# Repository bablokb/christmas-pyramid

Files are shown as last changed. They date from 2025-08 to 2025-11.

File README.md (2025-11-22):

A 3D-printed, Motor-driven Christmas Pyramid
============================================

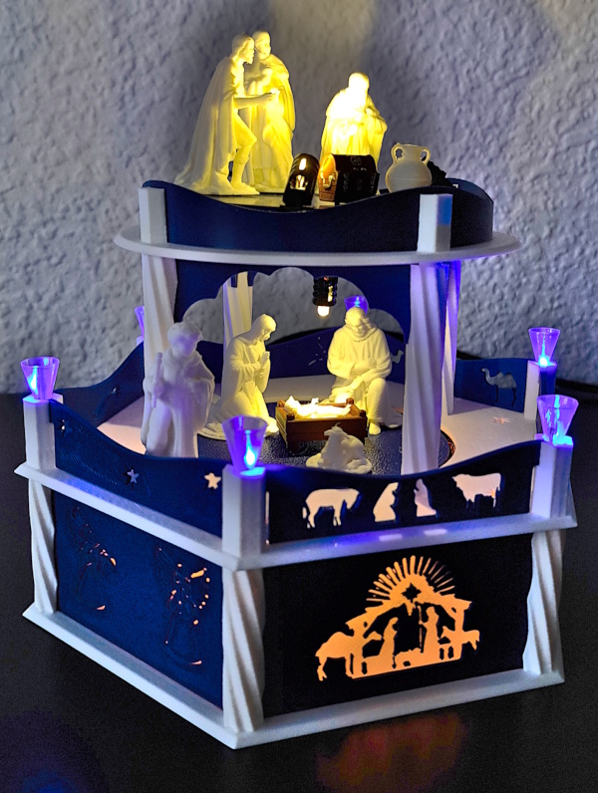
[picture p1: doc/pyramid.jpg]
pyramid.mp4


Introduction
------------

This project is about building a christmas pyramid with a motor driven
turntable, lightning and music (click on the image above to see it in
action). There are three distinct parts: the electronics, the software
and the 3D-design. A fourth part, a selfmade pcb is also available,
but not necessary. I only use it because it minimizes cables.

The electronics uses cheap parts that are widely available. The software is
implemented in CircuitPython and mostly portable. The 3D build uses
easy to print parts that can be assembled without glue.

Besides the "big" version with multiple levels, a simplified version is
also available:

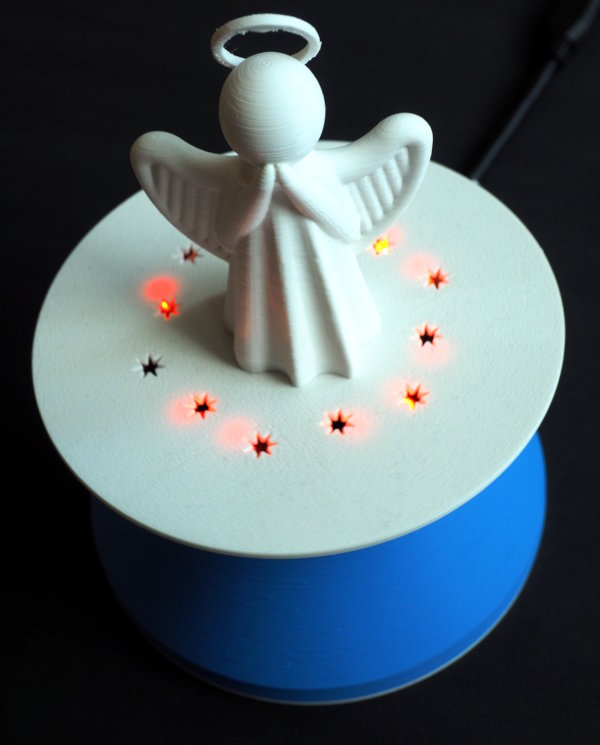
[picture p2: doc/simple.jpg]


This version only has three printed parts: the base, the wall and the
plate. It uses a neopixel-ring instead of LEDs, otherwise
it uses the same electronics as the normal version of the pyramid.

Details
-------

Read about

  - [Electronics](./doc/electronics.md)
  - [Software](./doc/software.md)
  - [3D-Printing](./doc/printing.md)
  - [Support-PCB](./doc/pcb.md)

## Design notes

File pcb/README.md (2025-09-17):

KiCAD Source Files for the Support PCB
======================================

For details, read [pcb.md](../doc/pcb.md).

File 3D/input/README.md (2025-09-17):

This file contains a number of remixes of existing models (see
[printing](../doc/printing.md)).

All models were flattened, centered and scaled for use as silhouttes
and cutouts for walls and fences.

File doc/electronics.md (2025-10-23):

Electronics
===========

The Motor
---------

The turntable is driven by a small 28BYJ-48 stepper motor (5V
version). Stepper motors are actually not the first choice for
continuous rotation, but since we need very low rpm values, this
option simplfies things. Another advantage is the fact that we can
drive this motor with 5V, so we only need a single power supply for
the motor and the microcontroller board.

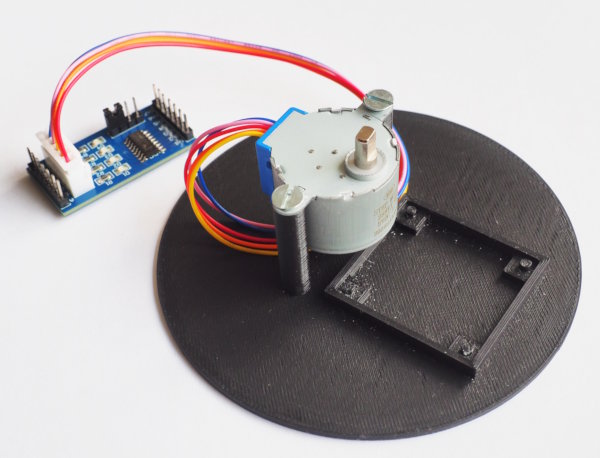
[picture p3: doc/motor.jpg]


The motor needs a driver board. It is usually sold together with an
uln2003a board. Make sure to buy the "blue" version with all seven
pins broken out. The board has seven channels, four of them are
necessary for the motor. The remaining three channels can be used to
drive LEDs.

Both the "blue" as the "green" driver boards have four useless LEDs
that blink when the mcu sends data. If necessary, just remove the LEDs
e.g. with pliers.

If you want to turn more than one level, you probably need a stronger
motor, e.g. a NEMA-17. Those motors also need a different voltage and
a different driver board. In this case it is better to supply the 5V
for the microcontroller from a step-down board.

The motor does not have to be in the center of the turntable but you
will need gears if not. OpenSCAD has a gears library that might be
useful in this case.

Lighting
--------

There are many options available to add some lighting. This implementation
uses three channels of the uln200a to drive 5V LEDs. Basic illumination
for the silhouettes uses standard 3mm LED-strips cut to the right length
(they can be cut and soldered every 25mm).

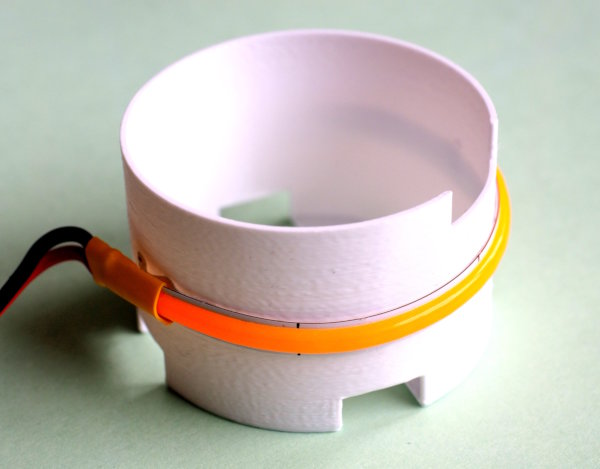
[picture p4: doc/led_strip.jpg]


For the remaining lights, normal flicker-LEDs are a good choice. They are
available pre-assembled with resistor and cables. Another option are
components from a Lego lighting kit. The LEDs use very thin wires which
makes assembly easy. The drawback are the connectors they use. It
is not trivial to attach them to a normal devboard, and even
attaching them to standard (lego-lighting) components is fiddly.

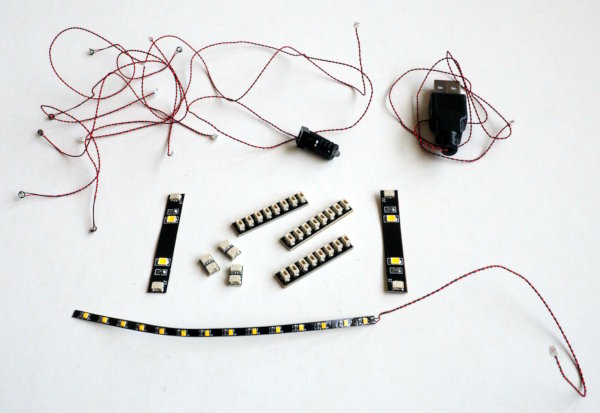
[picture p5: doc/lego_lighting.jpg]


The pyramid in this project makes heavy use of them to distribute
power to the upper levels through hallow posts.

Music
-----

The recommandation for music is to use a [DFPlayer
Mini](https://wiki.dfrobot.com/DFPlayer_Mini_SKU_DFR0299). This
breakout is not much larger than a SD-reader. It has a MP3-decoder and
an amplifier on board. The autonomous player takes load off the
microcontroller.  Two IOs enable basic operation (next/previous song
and volume up/down). All functions can be controlled using
UART-commands. Libraries for the DFPlayer are available for every
relevant language.

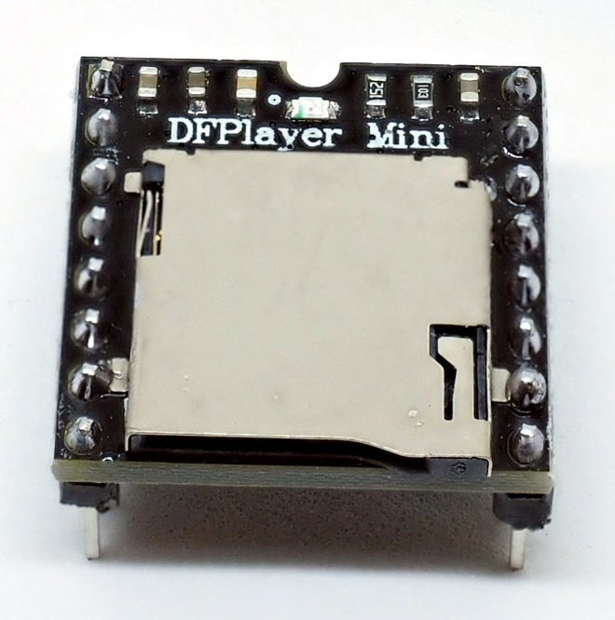
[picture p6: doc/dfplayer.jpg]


It seems that there are different version of the DFPlayer Mini around,
some are counterfeits. Problems with initialization have been
reported. On some (old?!) versions random playback does not seem to
work.

The alternative is to decode the MP3 in the microcontroller and output
I2S to a small I2S-DAC (e.g. the MAX98357A). While this does works it
has a number of drawbacks. At least with the ESP32-S2 which I use the
motor tends to stutter. A faster processor might not have this
problem. The second drawback is the larger number of pins needed (four
for the SD-card, four for the I2S-DAC and some more for buttons if you
want to control the playback). And finally a SD-breakout plus
amplifier is more expensive than the DFPlayer and both together need
two times the physical space.

The Microcontroller
-------------------

The mcu must provide enough digital IO pins and must be fast
enough. Something like the Pico should be fine. Depending on your
setup, you need

  - motor: 4 IO-pins
  - LEDs: 0-3 IO-pins
  - DFPlayer: 2 UART pins
  - Buttons: 3 IO pins

Since the DFPlayer provides two IOs, the IOs for the three buttons will
control the turntable speed (slower/faster) and pause the audio.
If you want to control more functions, you need more.

This project uses the Lolin-S2 Mini. It provides many pins on a small
footprint. As an added bonus, it could act as a webserver to enable
remote control via an app. This is an option that is not implemented.

Further Reading
---------------

Head on to [Software](./software.md) to read about the how to
drive the hardware.

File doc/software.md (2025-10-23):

The Software
============

The software is implemented in CircuitPython, but porting it to other
languages (especially MicroPython) should be straight forward.

The provided source-code is agnostic about the microprocessor that is
used. Since CircuitPython supports many different processors, you are
free to pick what you want (as long as you have enough IO-pins).

Read the section about configuration below to adapt the software to your
specific setup.

Installation
------------

Just copy everything below `src/` to your device. Note that `src/lib`
contains a number of precompiled libraries:

  - adafruit_pixelbuf
  - adafruit_ticks
  - asyncio
  - neopixel

These are CircuitPython version 9 libraries (also compatible
with version 10). You might want to update these libraries if you have
problems (the recommended way is to use circup).

Configuration
-------------

Use `src/config_pcb.py` or `src/config_breadboard.py` as a template
for your own configuration and change the import in `src/main.py`
accordingly.

Implementation Notes
--------------------

The hardware components (Motor, LEDs, music and buttons) are wrapped
by simple classes and controlled by asynchronous tasks. The main
program does not do much more than instantiating a task for every
hardware component and then starting all of them in parallel.

    motor = Motor(config.PINS_MOTOR,
                  config.GEAR_RATIO,
                  config.DIRECTION,
                  config.RPM,
                  config.DEBUG)
    player = Player(config.PINS_UART, config.VOLUME, config.DEBUG)
    buttons = Buttons(config.PINS_BUTTON, config.PINS_CB,
                      motor, player, config.DEBUG)
    leds = Leds(config.PINS_LED, config.DUTY_LED, config.DEBUG)

    stop_event = asyncio.Event()
    atexit.register(at_exit,stop_event,player)

    # start controller tasks and wait for end
    await asyncio.gather(buttons.run(0,stop_event),
                         motor.run(0,stop_event),
                         player.run(0.2,stop_event),
                         leds.run(0.5,stop_event)
                         )

As you can see, there is a stop-event that is triggered during
exit-processing in case of any exception (like a
keyboard-interrupt). This s useful for software development, sind in a
productive environment, stopping is done simply by pulling the power-plug.

The tasks themselves are also simple. The motor task for example just
starts the motor and then waits for the stop-event:

    async def run(self, delay, stop_event):
      """ create motor task """

      await asyncio.sleep(delay)
      self._motor = uln2003a.Uln2003aFullStep(*self._pins,
                                              self._gear_ratio,
                                              debug=self._debug)
      asyncio.create_task(self._motor.rotate(self._direction,self._rpm))
      await stop_event.wait()
      self._motor.stop()
      self._motor.deinit()

The button class uses the `keypad`-module from core CircuitPython
to catch and process any buttons that are pressed. The other wrapper
classes provide callbacks that are directly executed from the button-task.

The lighting uses a slightly modified version of the LED-animation
library from <https://github.com/jandelgado/jled-circuitpython>.

The libraries for the DFPlayer and the motor are from myself, see
<https://github.com/bablokb/circuitpyton-dfplayer> and
<https://github.com/bablokb/circuitpyton-uln2003a>.

Porting
-------

For MicroPython, porting should be simple. The DFPlayer library of
this project is a port of a MicroPython library. For the uln2003a you
will also find existing MicroPython libs, but AFAIK these do not support
async operations. A suitable LED-animation library should also be
available.

For C (Arduino) the situation should be similar. The original source
code of DFRobot for the DFPlayer was written for Arduino (but there
are others as well). The LED-animation library used in this project is
also available in a C version. And support for the uln2003 is also
available.

Further Reading
---------------

Head on to [3D-Printing](./printing.md) to read about the how the
pyramid is printed and assembled.

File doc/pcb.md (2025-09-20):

Support PCB for Electronic Components
=====================================

This PCB allows you to put all components on a small footprint.

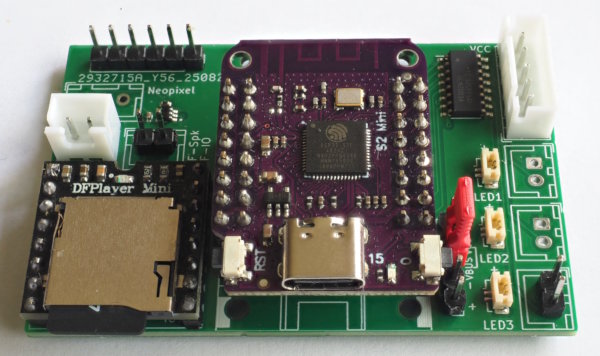
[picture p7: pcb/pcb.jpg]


On board:

  - uln2003a motor driver
  - level-shifter for a strand of neo-pixels
  - 3 SURS connectors for Lego-lighting

Connectors (THT):

  - Motor (JST-XH)
  - 3xLED (JST-XH)
  - Lolin S2-Mini
  - DFPlayer Mini
  - Speaker
  - 2 IOs from DFPlayer
  - 1x6 header with GND + 5 IOs (for external buttons)
  - 2x5 header with 2xGND, 2x3V3 + 6 IOs
  - 1x Grove I2C

This project neither uses the neo-pixel, the I2C-connector or the
optional 2x5 IO-header.

In the directory `production_files` you have ready to deploy files
for JLCPCB.

Schematic
---------

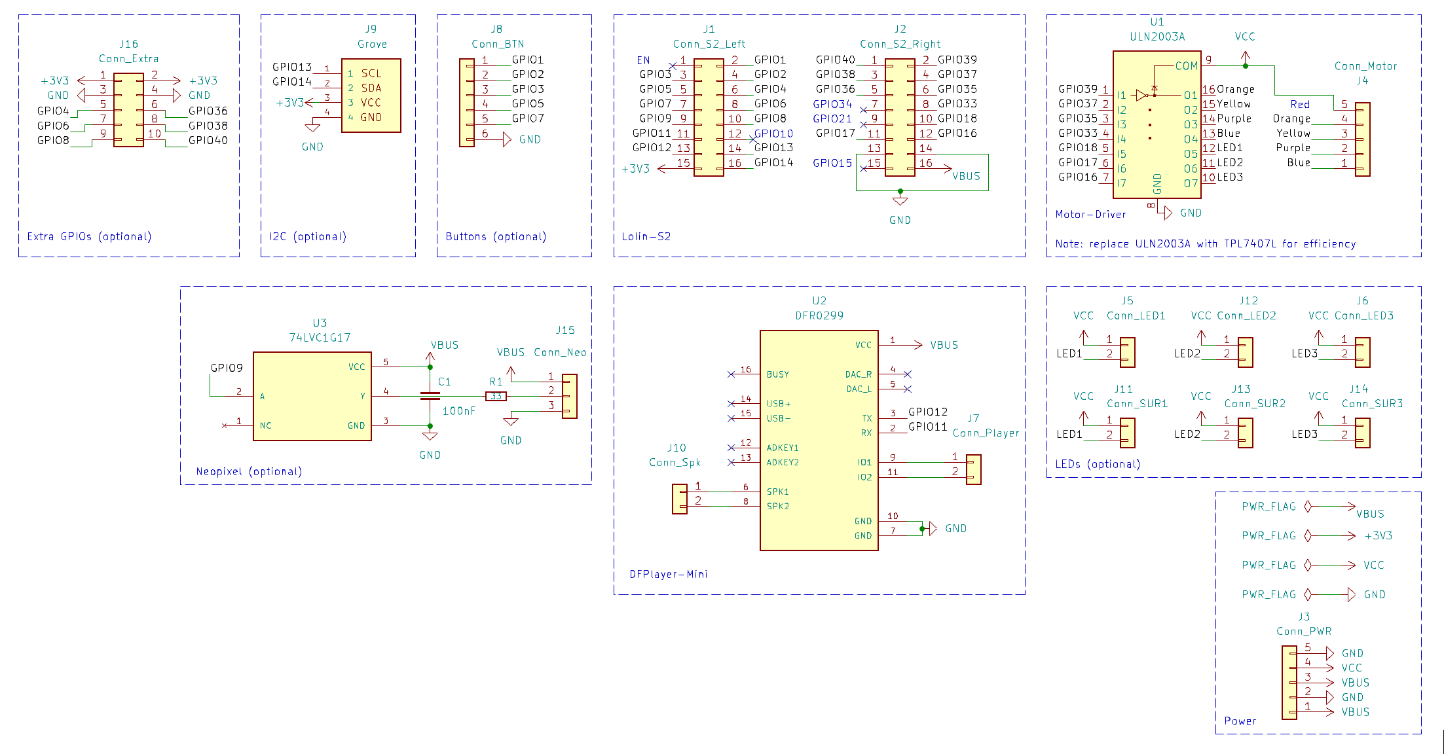
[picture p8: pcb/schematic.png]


Layout
------

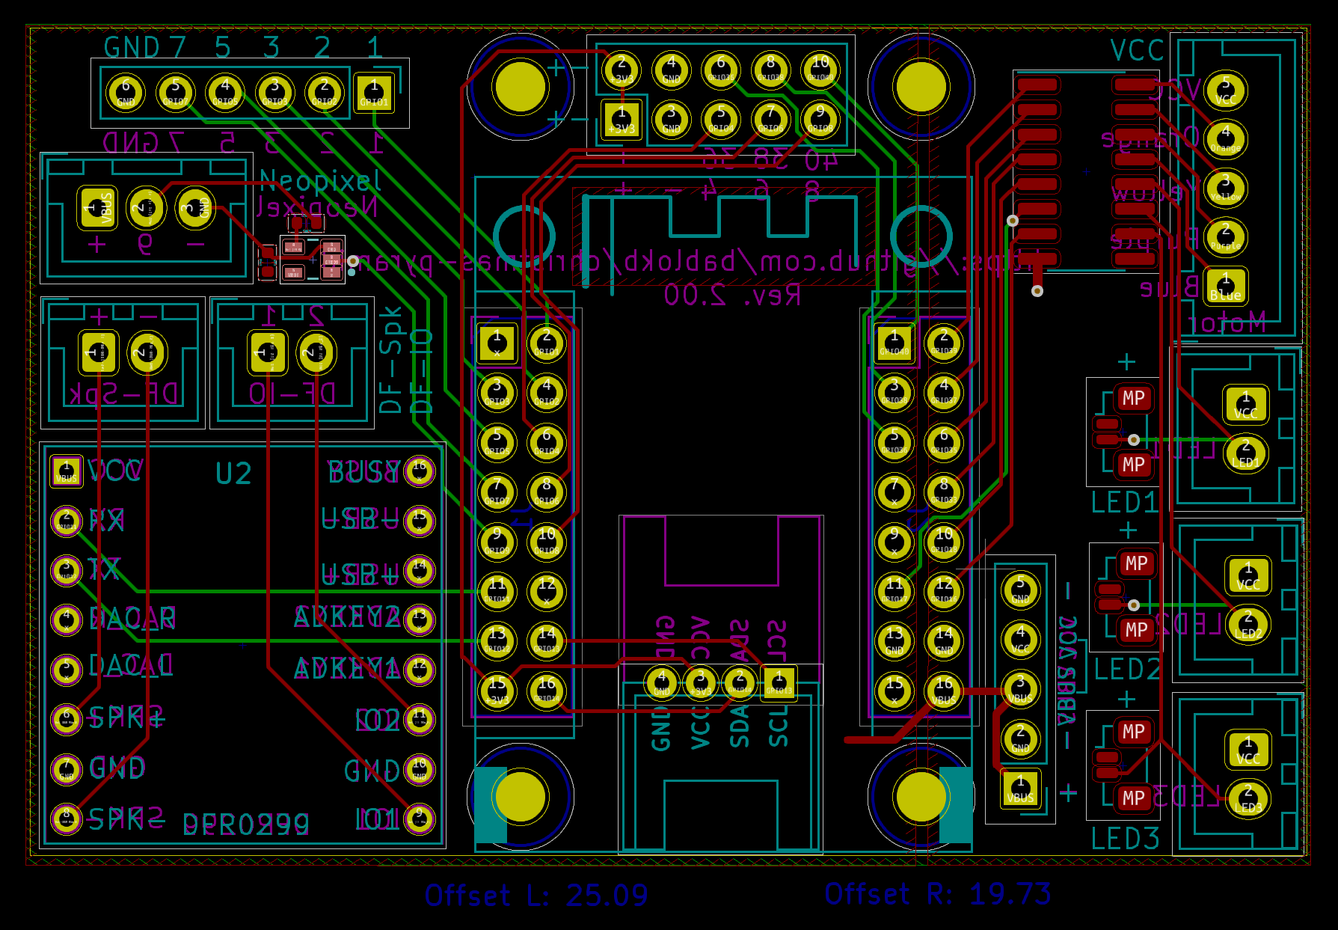
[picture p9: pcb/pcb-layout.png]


3D-View
-------

Note: there is no 3D-file for the SUR-Adapter, so this part
is missing in this image:

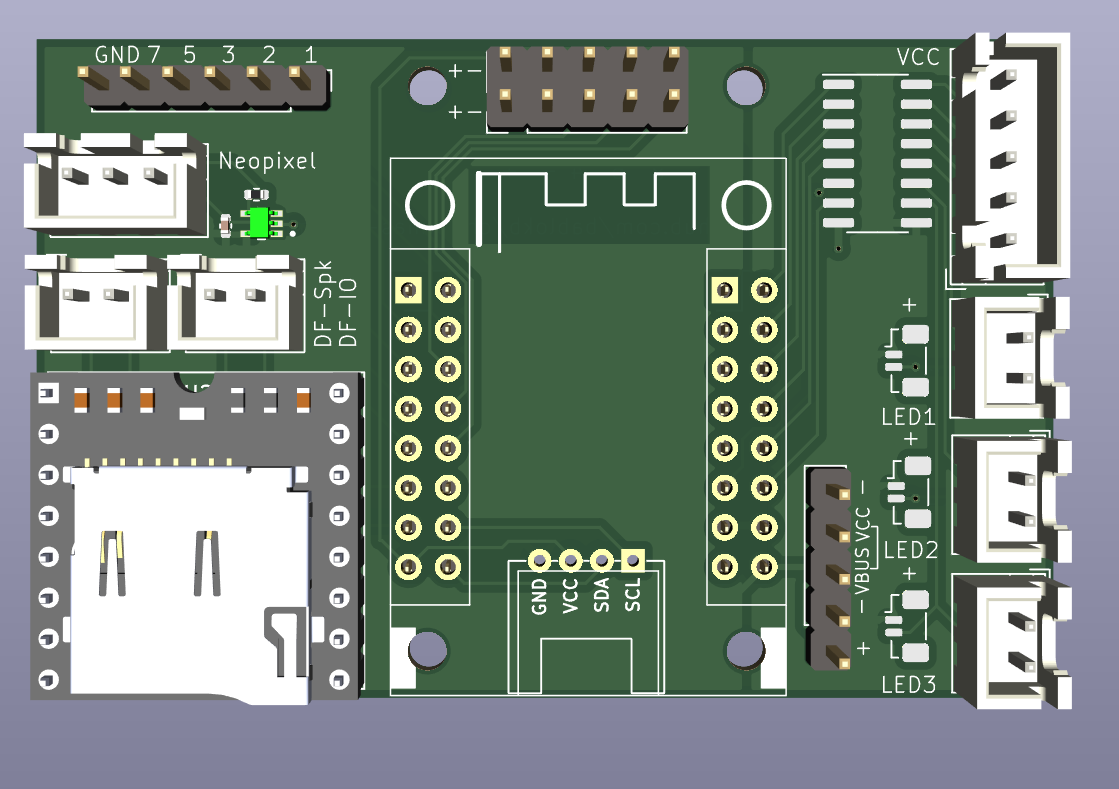
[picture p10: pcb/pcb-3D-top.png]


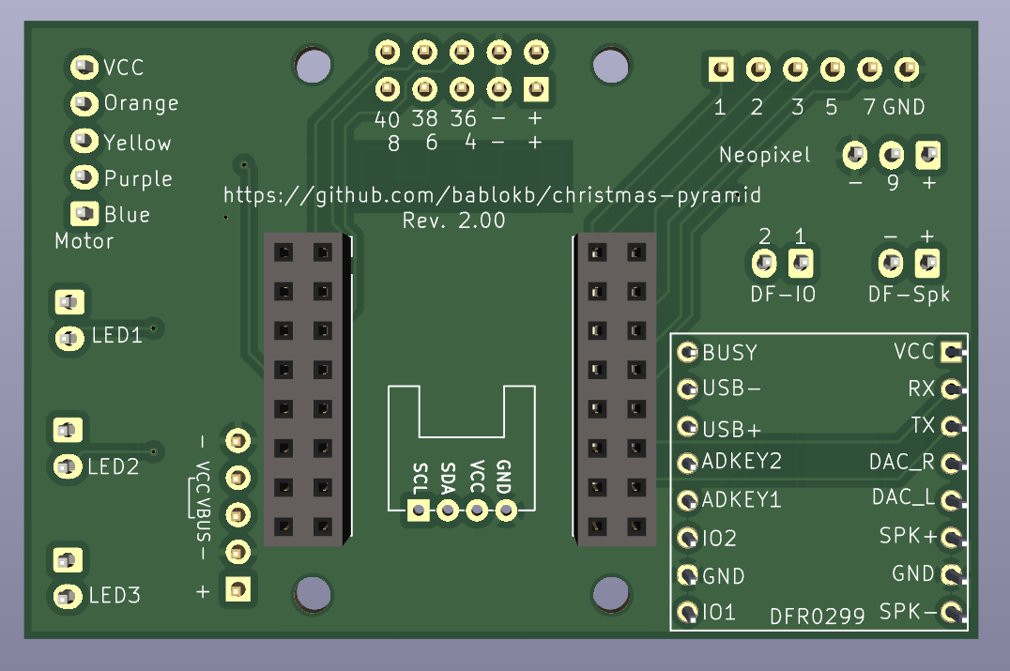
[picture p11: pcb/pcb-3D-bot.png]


License
-------

[![CC BY-SA 4.0][cc-by-sa-shield]][cc-by-sa]

This work is licensed under a
[Creative Commons Attribution-ShareAlike 4.0 International
License][cc-by-sa].

[][cc-by-sa]

[cc-by-sa]: http://creativecommons.org/licenses/by-sa/4.0/
[cc-by-sa-image]: https://licensebuttons.net/l/by-sa/4.0/88x31.png
[cc-by-sa-shield]:
https://img.shields.io/badge/License-CC%20BY--SA%204.0-lightgrey.svg

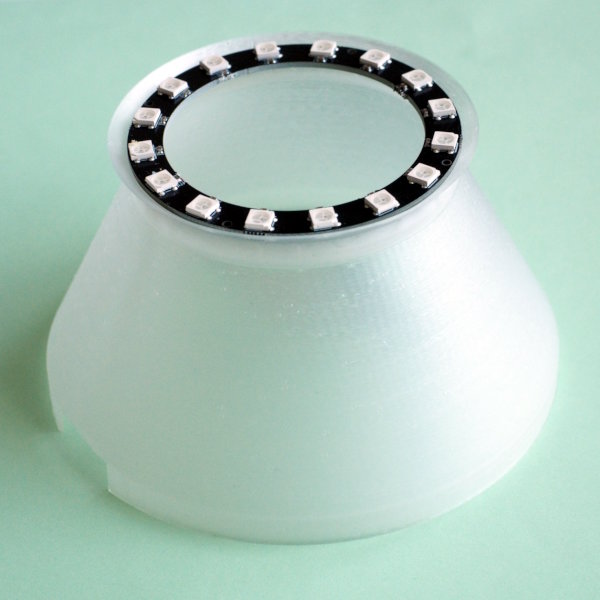
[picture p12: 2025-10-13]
doc/simple-wall.jpg

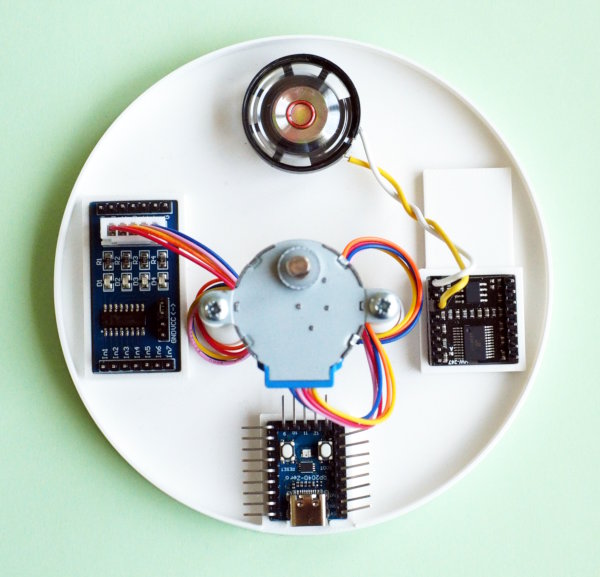
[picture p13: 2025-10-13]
doc/simple-base.jpg

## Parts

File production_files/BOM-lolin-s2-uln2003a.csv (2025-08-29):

Comment | Designator | Footprint | LCSC
100nF | C1 | C_0402_1005Metric | C1525
33 | R1 | R_0402_1005Metric | C25105
Conn_SUR1 | J11,J13,J14 | JST_SUR_BM02B-SURS-TF_1x02-1MP_P0.80mm_Vertical | C385130
74LVC1G17 | U3 | 74LVC1G17GW_125 | C426705
ULN2003A | U1 | SOP-16_3.9x9.9mm_P1.27mm | C7512

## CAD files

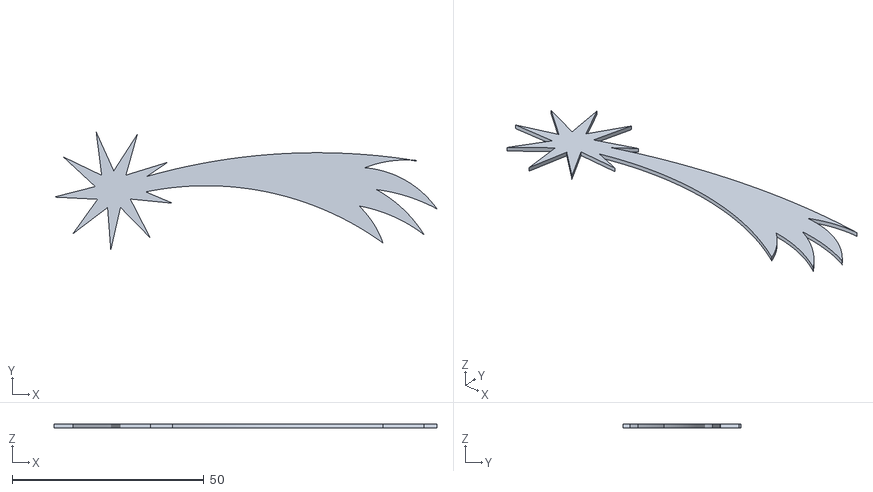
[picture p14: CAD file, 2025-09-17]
3D/input/star_of_bethlehem.stl
100.0 x 30.8 x 1.00

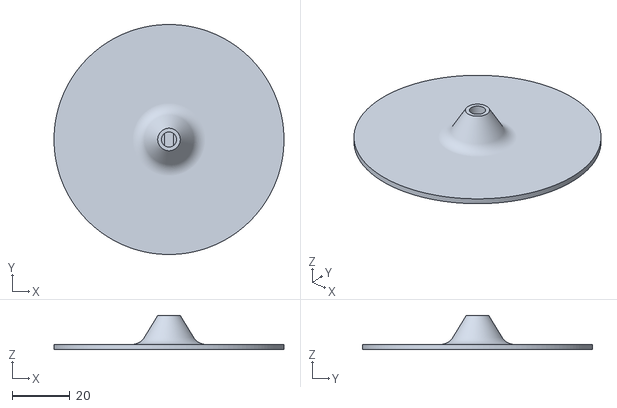
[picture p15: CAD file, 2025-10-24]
models/tt_plate.stl
79.5 x 79.5 x 11.8

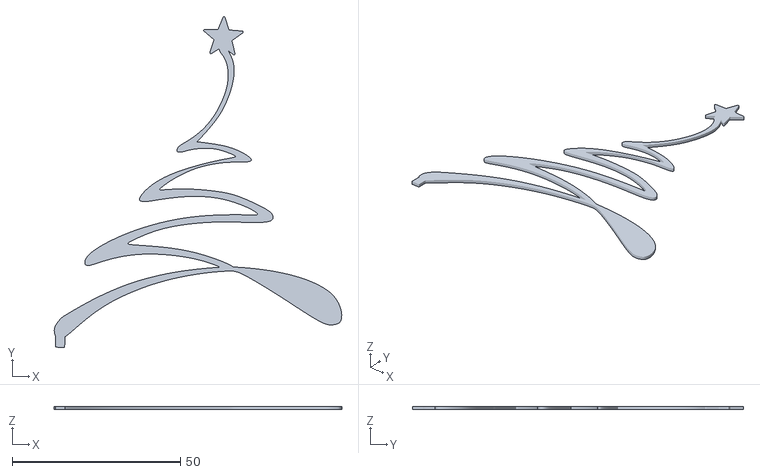
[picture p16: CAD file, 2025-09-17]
3D/input/tree_abstract.stl
85.5 x 98.4 x 1.00

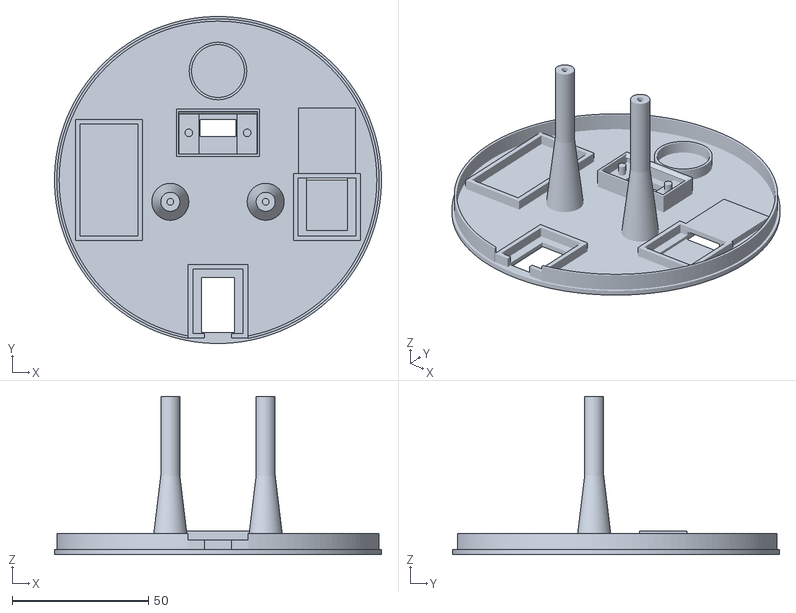
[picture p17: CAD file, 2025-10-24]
models/simple_base.stl
120.0 x 120.0 x 58.0

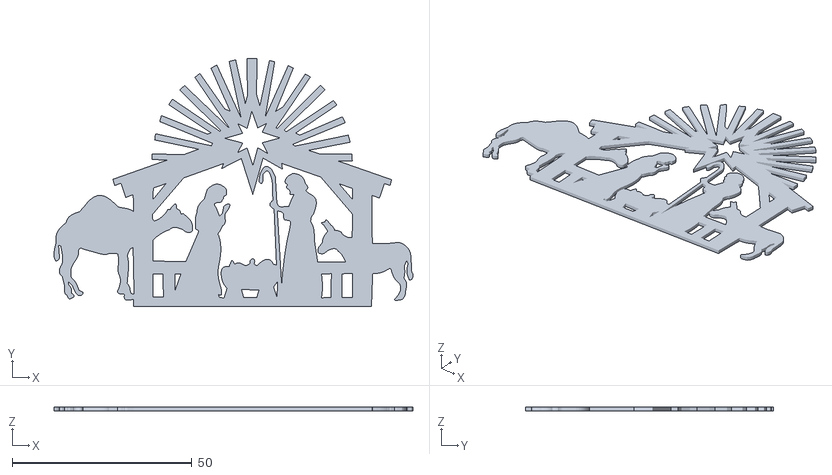
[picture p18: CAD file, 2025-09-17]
3D/input/nativity.stl
100.0 x 69.0 x 1.00

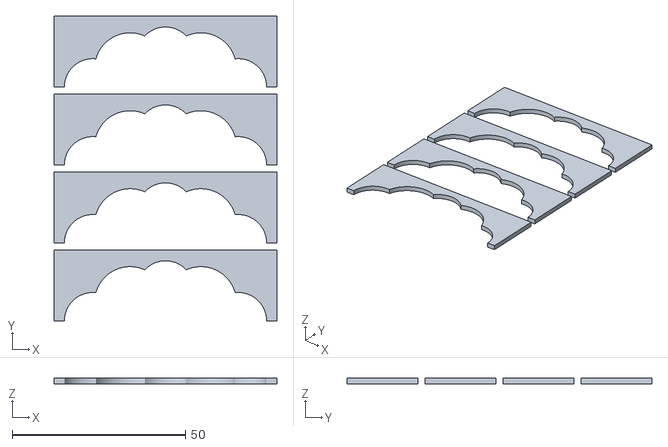
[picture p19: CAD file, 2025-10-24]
models/level1_walls.stl
64.4 x 88.0 x 1.60

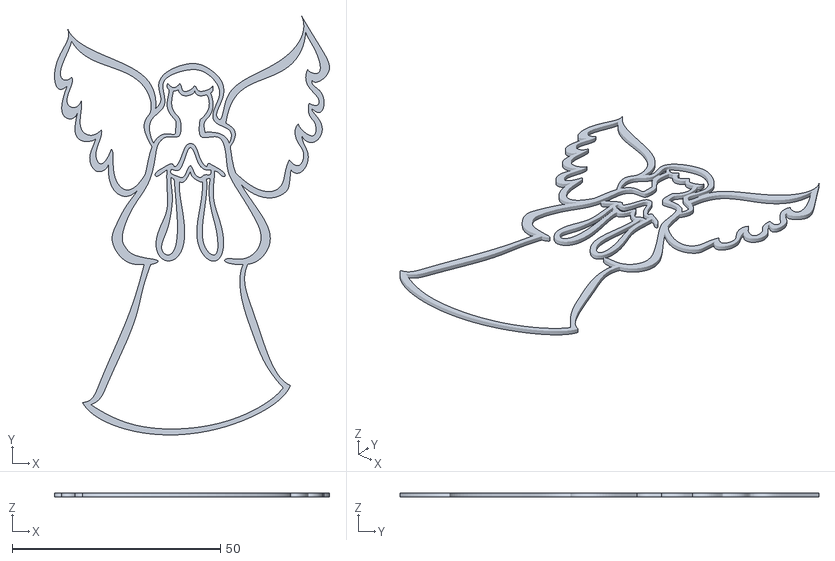
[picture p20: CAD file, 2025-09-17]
3D/input/angel_praying.stl
66.1 x 100.7 x 1.00

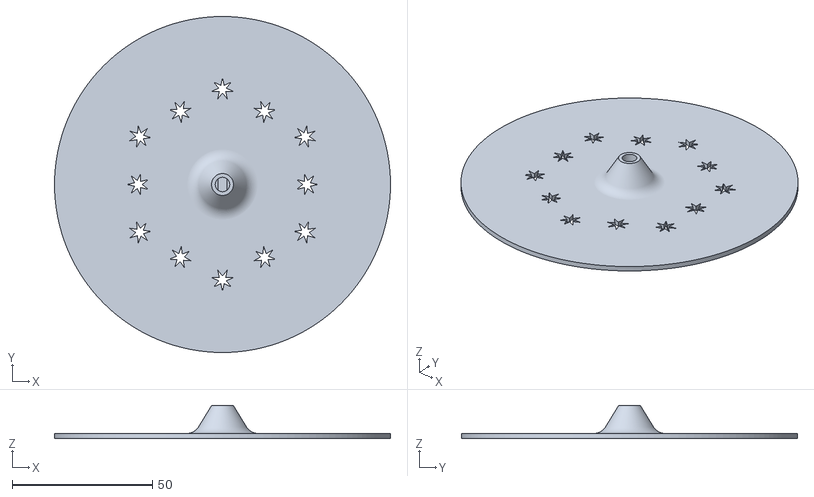
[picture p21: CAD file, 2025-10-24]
models/simple_plate.stl
120.0 x 120.0 x 11.8

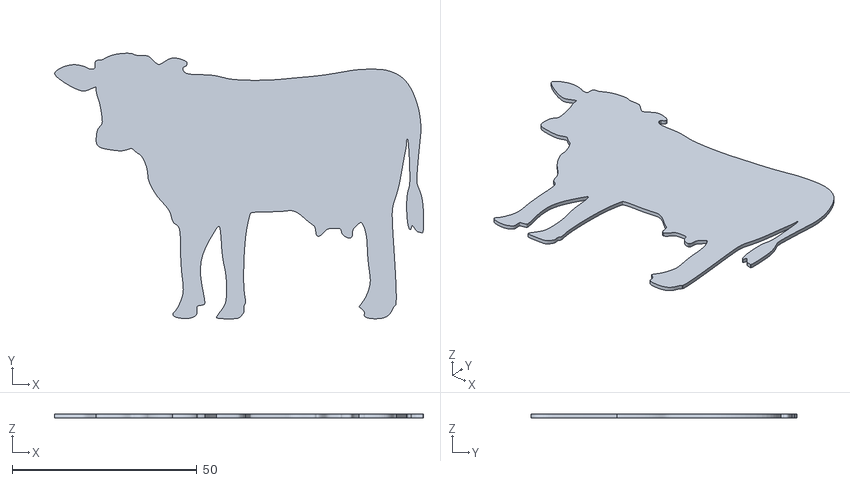
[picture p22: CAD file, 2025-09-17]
3D/input/cow.stl
100.0 x 72.0 x 1.00

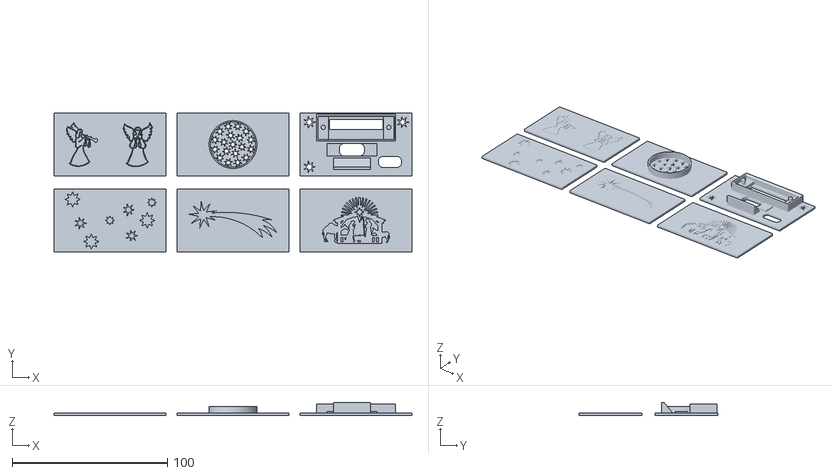
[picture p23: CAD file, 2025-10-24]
models/base_walls.stl
230.4 x 89.5 x 8.67

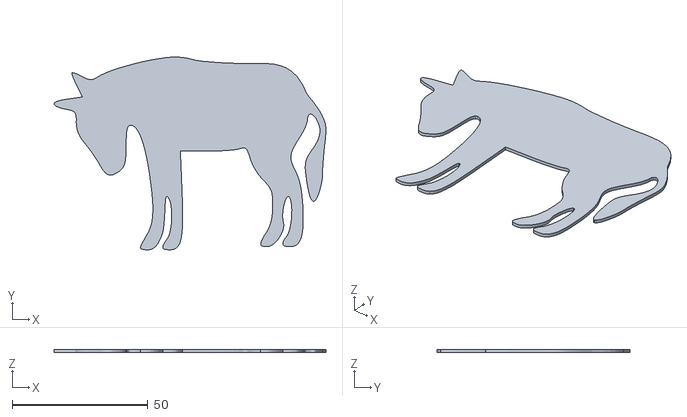
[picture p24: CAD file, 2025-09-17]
3D/input/donkey.stl
100.0 x 70.9 x 1.00

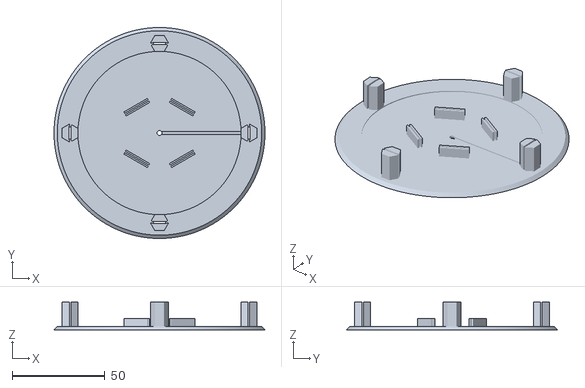
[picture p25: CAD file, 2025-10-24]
models/level2.stl
113.9 x 113.9 x 15.0

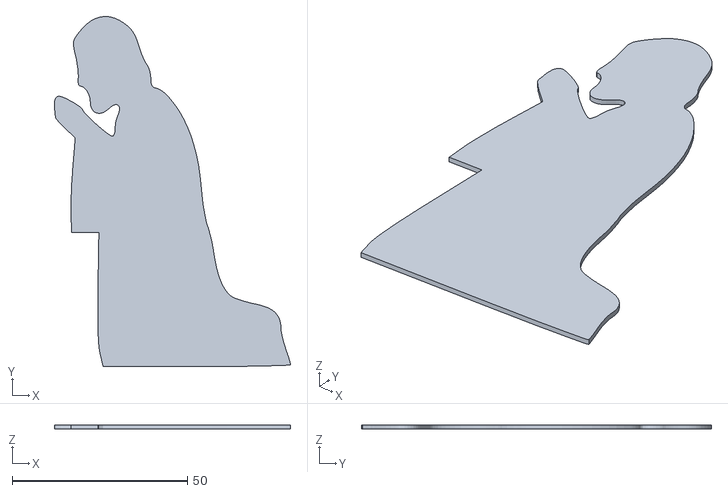
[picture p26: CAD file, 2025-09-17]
3D/input/joseph.stl
67.5 x 100.0 x 1.00

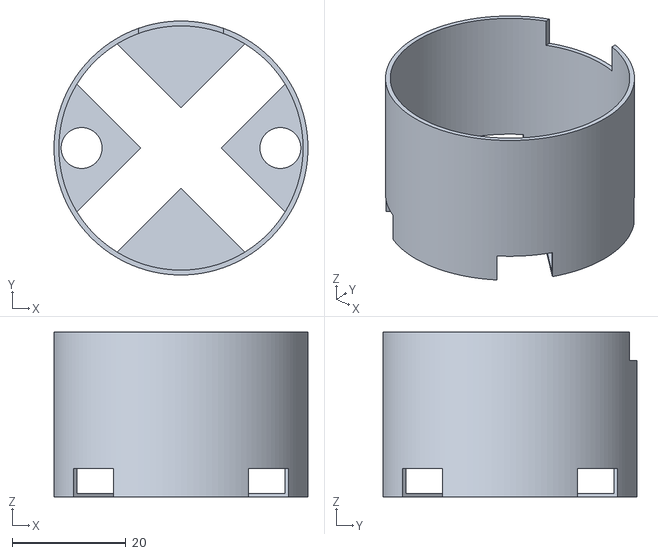
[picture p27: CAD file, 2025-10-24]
models/led-strip-holder.stl
44.7 x 44.7 x 29.0

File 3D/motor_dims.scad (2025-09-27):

// -----------------------------------------------------------------------------
// 3D-Model (OpenSCAD): dimensions of moter.
//
// Author: Bernhard Bablok
// License: GPL3
//
// https://github.com/bablokb/christmas-pyramid
// ---------------------------------------------------------------------------

include <dimensions.scad>

// ---------------------------------------------------------------------------
// motor support dimensions

z_motor = 19;                      // size of motor without shaft

do_support = 7;                    // motor support outer diameter
di_support = 2.5;                  // motor support inner diameter (screw: 2.6)
ox_support = 17.5;                 // offsets of support: 35/2
oy_support = -8;

// ---------------------------------------------------------------------------
// motor shaft dimensions

d1_shaft = 9 + gap;     // shaft at bottom (motor-side, circle-shaped)
z1_shaft = 1.5;
d2_shaft = 5 + gap;     // shaft above bottom (circle-shaped)
z2_shaft = 4;
d3_shaft = 3 + gap;     // shaft at top (flat)
z3_shaft = 6;

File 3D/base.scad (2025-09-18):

// -----------------------------------------------------------------------------
// 3D-Model (OpenSCAD): Base level of the pyramid.
//
// Author: Bernhard Bablok
// License: GPL3
//
// https://github.com/bablokb/christmas-pyramid
// ---------------------------------------------------------------------------

include <BOSL2/std.scad>
include <shared.scad>
include <pcb_holder.scad>

ch_off = 0.6 * x_bottom;   // cable-holder offset

// --- module post: cylinder with hole   -------------------------------------

module motor_post() {
  tube(h=z_support,od=do_support,id=di_support, anchor=BOTTOM+CENTER);
}

// --- module motor-support   ------------------------------------------------

module motor_support() {
  move([+ox_support,oy_support,0]) motor_post();
  move([-ox_support,oy_support,0]) motor_post();
}

// --- posts for next level of pyramid   -------------------------------------

module post(h,r,twist=120) {
  difference() {
    union() {
      // post
      if ($preview) {
        cyl(h,r, anchor=BOTTOM+CENTER);
      } else {
        // supershape is very slow in rendering
        // linear_extrude(h,twist=twist) supershape(.5,m1=8,n1=1,r=r);
        linear_extrude(h,twist=twist) star(n=8, r=r, step=2);
      }
      // cone above post
      zmove(h-fuzz) cyl(zc_bottom,pc_bottom, anchor=BOTTOM+CENTER);
    }
    // cutouts for walls
    zrot(30) ymove(pr_bottom-wxc_bottom)
        cuboid([wz_bottom+gap,10,h+b+fuzz], anchor=BOTTOM+FRONT);
    zrot(-30) ymove(-pr_bottom+wxc_bottom)
        cuboid([wz_bottom+gap,10,h+b+fuzz], anchor=BOTTOM+BACK);
    // cutouts for LED-cable
    zrot(-90) zmove(0.67*h+b) xrot(-8)
        cuboid([wz_bottom+gap,10,h/3+b+fuzz], anchor=BOTTOM+BACK);
  }
}

// --- a single cable-holders   ----------------------------------------------

module cable_holder() {
  x_holder = 3*b; y_holder = 2*b; z_holder = 4*b;
  zmove(x_holder/2+w4) yrot(90)
    rect_tube(isize=[x_holder,y_holder],wall=w4,h=z_holder,anchor=CENTER);
}

// --- all cable-holders   ---------------------------------------------------

module cable_holders() {
  xflip_copy() {
    zrot(0) xmove(ch_off) cable_holder();
    yflip_copy()
      zrot(-60)
        zrot(-30,cp=[x_bottom-po_bottom,0,0])
          xmove(ch_off) cable_holder();
  }
}

// --- wall cutout   ---------------------------------------------------------

module wall_cutout() {
  zmove(b-wyc_bottom)
    linear_extrude(wyc_bottom+fuzz)
      ring(n=6,r=x_bottom-po_bottom-wz_bottom/2-gap,ring_width=wz_bottom+2*gap);
}

// --- base plate   ----------------------------------------------------------

module base() {
  // base-plate
  r_ring = 2*ox_support;
  w_ring = 5;
  difference() {
    regular_prism(6,h_bottom,x_bottom,chamfer2=c_bottom,
            anchor=BOTTOM+CENTER);
    wall_cutout();
    zmove(-fuzz) ymove(oy_support)
      linear_extrude(h_bottom+2*fuzz)
       ring(r=r_ring, ring_width=w_ring, full=false, angle=[180,360]);
  }
  // support for motor
  motor_support();
  // pcb-holder, moved and rotated to the back side
  ymove(y_bottom - pcb_holder_dim(y_pcb)/2 - po_bottom + gap)
    zrot(180)
      pcb_holder_special(x_pcb=x_pcb,   y_pcb=y_pcb,
                 xl_screw = xl_pcb, xr_screw = xr_pcb, y_screw = ys_pcb);
  // posts for the next level
  for (r = [0:60:300]) {
    zrot(r) xmove(x_bottom-po_bottom) post(z_bottom,pr_bottom);
  }
  // cable-holders
  cable_holders();
}

// --- final shape   ---------------------------------------------------------

base();
//post(z_bottom,pr_bottom);
//pcb_holder_special(x_pcb=x_pcb,   y_pcb=y_pcb,
//                   xl_screw = xl_pcb, xr_screw = xr_pcb, y_screw = ys_pcb);
//cable_holder();

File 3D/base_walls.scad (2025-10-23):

// ---------------------------------------------------------------------------
// 3D-Model (OpenSCAD): Walls for base-segment.
//
// Print walls with silhouette (all except pcb and speaker) with a
// color-change after three layers. The first three layers should use
// transparent PLA, the other layers in the color you like.
//
// Author: Bernhard Bablok
// License: GPL3
//
// https://github.com/bablokb/christmas-pyramid
// ---------------------------------------------------------------------------

include <BOSL2/std.scad>
include <shared.scad>
include <pcb_holder.scad>
include <button_holder.scad>

h_cutout = 1.2;             // six layers a 0.2
rs_speaker = 3;             // stars for speaker
d_speaker  = 29;            // speaker itself
h_speaker  =  4.4;          // height of speaker

x_usb  = 16;                // size of USB-C
xo_usb = (xr_pcb-xl_pcb)/2; // offset from center
y_usb  =  8;
yo_usb = 13;                // offset from bottom

x_sd  =  15;                // size of SD-cutout
xo_sd =  xo_usb+24.5;       // offset from center
y_sd  =   7;                // printed, will be vertical later
yo_sd =   5;                // offset SD-card above PCB

x_holder  = 24;             // pcb-holder
yo_holder = pcb_holder_z() - b + wyc_bottom;   // pcb-level
z_holder  = 7 + w4;

// --- base wall   -----------------------------------------------------------

module wall() {
  cuboid([wx_bottom,wy_bottom,wz_bottom], anchor=BOTTOM+CENTER);
}

// --- wall for PCB   --------------------------------------------------------

module wall_pcb() {
  off_corners = 6;
  h_cutouts = wz_bottom+2*fuzz;
  difference() {
    union() {
      wall();
      // addition for USB-C cutout
      move([xo_usb,-wy_bottom/2+y_usb/2+yo_usb,wz_bottom-fuzz])
        cuboid([2*x_usb,y_usb-2*fuzz,0.75*w4], anchor=BOTTOM+CENTER);
    }
    // cutouts
    // SD-card
    move([xo_sd,-wy_bottom/2+yo_holder+yo_sd,-fuzz])
      cuboid([x_sd,y_sd,h_cutouts],
              rounding=3, edges="Z",anchor=BOTTOM+CENTER);
    // USB-C (not centered on pcb!)
    move([xo_usb,-wy_bottom/2+y_usb/2+yo_usb,-fuzz])
      cuboid([x_usb,y_usb,wz_bottom+h_cutouts],
             rounding=3, edges="Z", anchor=BOTTOM+CENTER);
    // cutout buttons
    zmove(-fuzz)
      ymove(wy_bottom/2-y_btn_holder/2-wyc_bottom)
        hull() btn_holder(wz_bottom, 5);

    // for some air-flow
    move([-wx_bottom/2+off_corners,-wy_bottom/2+off_corners,-fuzz])
      linear_extrude(h_cutouts) star(n=7, r=4, step=3);
    move([-wx_bottom/2+off_corners,+wy_bottom/2-off_corners,-fuzz])
      linear_extrude(h_cutouts) star(n=7, r=4, step=3);
    move([+wx_bottom/2-off_corners,+wy_bottom/2-off_corners,-fuzz])
      linear_extrude(h_cutouts) star(n=7, r=4, step=3);
  }
  // pcb-holder
  move([xo_usb,-wy_bottom/2+yo_holder,-fuzz])
    color("blue") prismoid(size1=[x_holder,z_holder],
             size2=[x_holder,w4],
             shift=[0,-z_holder/2+w4/2], h=z_holder, anchor=BOTTOM+FRONT);
  // button-holder
  ymove(wy_bottom/2-y_btn_holder/2-wyc_bottom) btn_holder(wz_bottom, 5);
}

// --- wall for speaker   ----------------------------------------------------

module wall_speaker() {
  difference() {
    wall();
    // cutouts stars
    move([0,0,-fuzz])
      linear_extrude(wz_bottom+2*fuzz) star(n=7, r=rs_speaker, step=3);
    for (i = [2:2:4]) {
      for (r = [0:120/i:360]) {
        move([0,0,-fuzz])
          zrot(r+(i-1)*15) ymove(i*rs_speaker)
            linear_extrude(wz_bottom+2*fuzz) star(n=7, r=rs_speaker, step=3);
      }
    }
  }
  zmove(wz_bottom-fuzz) tube(h=h_speaker, id=d_speaker, wall=w2,
                             anchor=BOTTOM+CENTER);
}

// --- wall with nativity scene   --------------------------------------------

module wall_nativity() {
  factor = 0.6*wx_bottom/100;
  difference() {
    wall();
    // cutouts
    zmove(b-h_cutout+fuzz)
        scale([factor,factor,h_cutout])
          import("input/nativity.stl");  // dim: 100x69.2x1
  }
}

// --- wall with star of Bethlehem   -----------------------------------------

module wall_bethlehem() {
  factor = 0.8*wx_bottom/100;
  difference() {
    wall();
    // cutouts
    zmove(b-h_cutout+fuzz)
        scale([factor,factor,h_cutout]) zrot(-10)
          import("input/star_of_bethlehem.stl");  // dim: 100x30.8x1
  }
}

// --- wall with angels   ---------------------------------------------------

module wall_angels() {
  factor = 0.7*wy_bottom/100;
  difference() {
    wall();
    // cutouts
    xmove(-wx_bottom/4) zmove(b-h_cutout+fuzz)
        scale([factor,factor,h_cutout])
          import("input/angel_trompet.stl");  // dim: 70.5x100x1
    xmove(+wx_bottom/4) zmove(b-h_cutout+fuzz)
        scale([factor,factor,h_cutout])
          import("input/angel_praying.stl");  // dim: 66.1x100x1
  }
}

// --- wall with stars   -----------------------------------------------------

module wall_stars(step=3) {
  difference() {
    wall();
    // cutouts: randomly placed stars
    move([-wx_bottom/3+5,-wy_bottom/6+5,b-h_cutout+fuzz])
      linear_extrude(h_cutout) star(n=7, r=4, step=step);
    move([-wx_bottom/3,+wy_bottom/3,b-h_cutout+fuzz])
      linear_extrude(h_cutout) star(n=8, r=5, step=step);
    move([-wx_bottom/6,-wy_bottom/3,b-h_cutout+fuzz])
      linear_extrude(h_cutout) star(n=8, r=5, step=step);
    move([0,0,b-h_cutout+fuzz])
      linear_extrude(h_cutout) star(n=8, r=3, step=step);
    move([+wx_bottom/6,+wy_bottom/6,b-h_cutout+fuzz])
      linear_extrude(h_cutout) star(n=7, r=4, step=step);
    move([+wx_bottom/3,0,b-h_cutout+fuzz])
      linear_extrude(h_cutout) star(n=8, r=5, step=step);
    move([+wx_bottom/3+3,+wy_bottom/3-2,b-h_cutout+fuzz])
      linear_extrude(h_cutout) star(n=8, r=3, step=step);
    move([+wx_bottom/6+2,-wy_bottom/6-3,b-h_cutout+fuzz])
      linear_extrude(h_cutout) star(n=7, r=4, step=step);

  }
}

// --- main   ----------------------------------------------------------------

distribute(l=1.2*wy_bottom, dir=BACK) {
  distribute(l=2.2*wx_bottom) {
    wall_stars();
    wall_bethlehem();
    wall_nativity();
  }
  distribute(l=2.2*wx_bottom) {
    wall_angels();
    wall_speaker();
    wall_pcb();
  }
}

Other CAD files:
3D/input/tree_with_star.stl
models/simple_wall.stl
3D/input/mary.stl
models/level2_plate.stl
3D/button_holder.scad
3D/dimensions.scad
3D/input/angel_trompet.stl
3D/input/camel.stl
3D/input/camel_sitting.stl
3D/led-strip-holder.scad
3D/level1.scad
3D/level1_fences.scad
3D/level1_walls.scad
3D/level2.scad
3D/level2_fence.scad
3D/pcb_holder.scad
3D/shared.scad
3D/simple_base.scad
3D/simple_plate.scad
3D/simple_shared.scad
3D/simple_wall.scad
3D/tt_plate.scad
models/base.stl
models/lamp_shades.stl
models/level1.stl
models/level1_fences.stl
models/level2_fence.stl

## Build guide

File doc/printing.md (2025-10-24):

3D Design and Printing
======================

The pyramid itself was created using OpenSDAD. Some existing models were
reused, mainly for cutouts and silhouettes. You will find all links below.



Architecture
------------

The pyramid (currently) has a base and two additional levels.  The
base and the levels are printed as skeletons without
walls/fences. These are printed separately. This allows for different
colors, makes silhouettes possible and also helps during assembly.

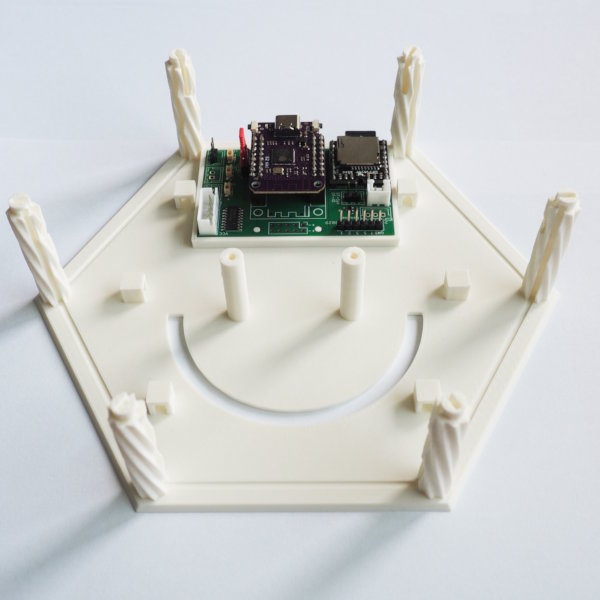
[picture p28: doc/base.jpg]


The basic geometric form is a regular hexagon. The side of the hexagon
is the same as the outer-radius, this makes calculations easy. All
major dimensions are a function of this size. The pyramid in the picture
was printed with a size of 85mm. Most printers should handle sizes up to
100mm which gives a diameter of 200mm.

There is a file called [`3D/dimensions.scad`](../3D/dimensions.scad)
and a file called [`3D/shared.scad`](../3D/shared.scad).  Both define
dimensions for the print. The first one sets generic dimensions which
depend on your printer (e.g. `w4`: optimal width for a 4-perimeter
wall). The second file has all the application level sizes.

Depending on the electronic-parts you are using, you will most certainly
need to modify the base-level, the wall for the speaker and the
wall for the buttons/sd-card/USB-connector.

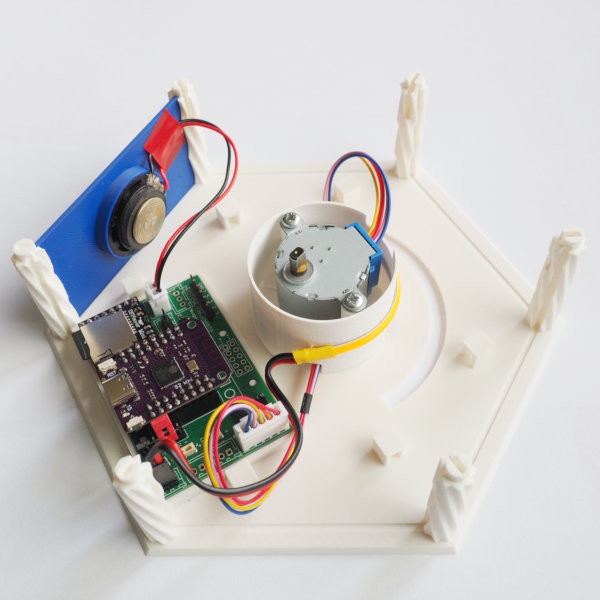
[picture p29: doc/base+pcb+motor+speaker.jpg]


Mapping of OpenSCAD-files to Models
-----------------------------------

Base:

  - base.scad
    - base.stl
  - base_walls.scad
    - base_walls.stl
  - led-strip-holder.scad
    - led-strip-holder.stl

Level 1:

  - level1.scad
    - level1.stl
    - lamp_shades.stl
    - tt_plate.stl
  - level1_walls.scad
    - level1_walls.stl
  - level1_fences.scad
    - level1_fences.stl

Level 2:
  - level2_fence.scad
    - level2_fence.stl
  - level2.scad
    - level2.stl
    - level2_plate.stl

Simple Version:

  - simple_base.scad
    - simple_base.stl
  - simple_wall.scad
    - simple_wall.stl
  - simple_plate.scad
    - simple_plate.stl

Filaments
---------

I used the following filaments:

  - BambuLab: Matte Ivory White (PLA)
  - Filament.de: Königsblau (PLA, royal blue)
  - Filament.de: Kastanienbraun (PLA, chestnut)
  - Filament.de: Natur (PLA, transparent)
  - Filament.de: Weiß (PETG, white)

Other filaments will certainly also work well, but you might have to
tweak some settings to get dimensions right.

Printing Hints
--------------

Most parts of the pyramid were printed with PLA and a standard nozzle,
with a layer height of 0.2mm. There are a few exceptions though.



The led-strip holder was printed with PETG for higher thermal stability.
The round level2-fence was printed with a layer hight of 0.10mm, as were
the nativity figures.

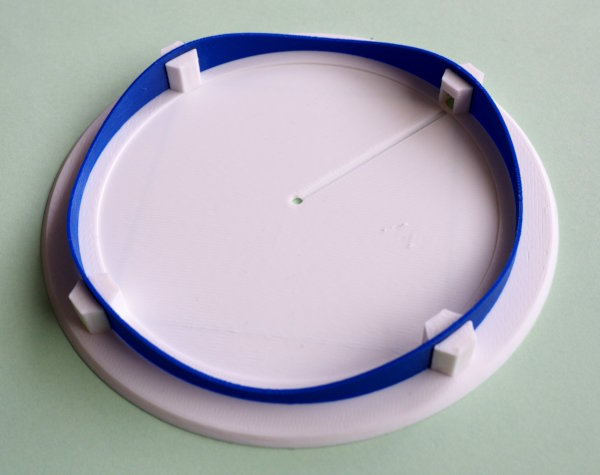
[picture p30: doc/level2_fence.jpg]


For the silhouettes I printed the first three layers with transparent
PLA, the rest was printed in blue. You need to add a color change
in the slicer after the third layer.

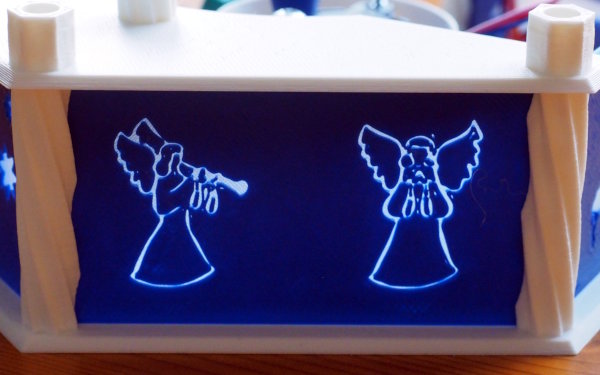
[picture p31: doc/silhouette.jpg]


Cutouts were printed as is. The challenge was to find suitable models
that don't have "islands" within the cutout.

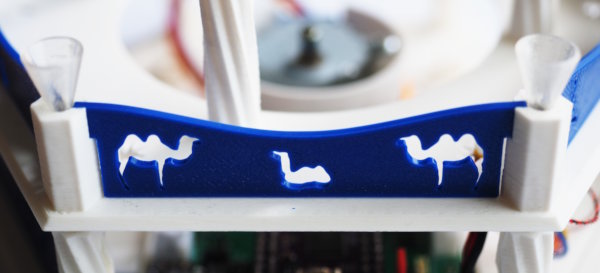
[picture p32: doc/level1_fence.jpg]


The little lamp-shades on level1 were printed in vase-mode without top
and bottom, again using transparent PLA. Since version 2.9.2
Prusa-Slicer supports sequential printing, so I could print all
lamp-shades in one go. This greatly reduces the overhead time since
bed-leveling is only needed once.

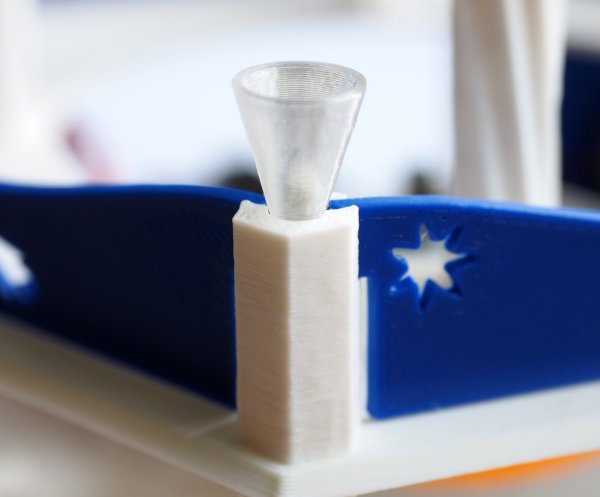
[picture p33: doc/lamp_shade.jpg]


The nativity figures were downscaled to 40% and printed with a layer
height of 0.15mm using tree supports (Prusa-Slicer calls this
"natural" supports). Removing the supports was not difficult, but you
need to take great care not to break anything. The only thing that did
not survive was the rod of the young shepard. But this is due to
downscaling, the rod is just too thin at 40%.

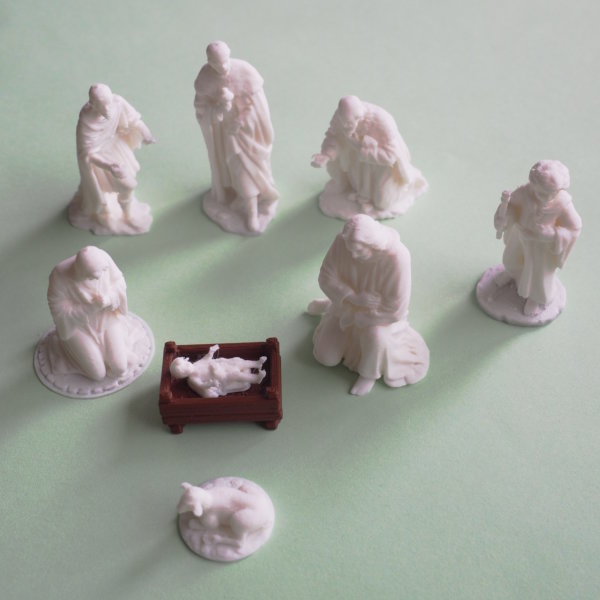
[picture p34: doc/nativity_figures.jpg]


Models
------

This project uses a number of models from other authors. The nativity
figures were used as is (except downscaling). The other models were used
for the walls and fences for cutouts and silhouettes. They were
flattened (linear projection) and resized for this purpose. The remixes
are in the directory [3D/input](../3D/input/README.md).

All models used allow remixing. See the links for details. One model has been
deleted.

Nativity Figures by [Peter Farell](https://www.printables.com/@PeterFarell):

  - Mary: <https://www.printables.com/model/1064402-nativity-mary>
  - Joseph: <https://www.printables.com/model/1064354-nativity-joseph>
  - Baby Jesus and manger: <https://www.printables.com/model/1064779-nativity-swaddled-baby-jesus-and-manger-set>
  - Wisemen: <https://www.printables.com/model/1049972-nativity-magi-wise-men>
  - Young shephard: <https://www.printables.com/model/1065406-nativity-young-shepherd-boy>
  - Shephard: <https://www.printables.com/model/1064471-nativity-shepherd>
  - Sheep: <https://www.printables.com/model/1064503-nativity-sheep-set>

[Base walls](../3D/base_walls.scad):

  - Nativity scene: <https://www.printables.com/model/1117975-nativity-set>
  - Comet star (star of Bethlehem): <https://www.thingiverse.com/thing:4691295>
  - Angels: <https://www.printables.com/model/7671-angel-ornaments-for-your-window>

[Level1 fences](../3D/level1_fences.scad):

  - Comet star (star of Bethlehem): <https://www.thingiverse.com/thing:4691295>
  - Christmas tree (with star): <https://www.printables.com/model/333927-christmastree>
  - Christmas tree (abstract): <https://www.printables.com/model/102859-christmas-tree>
  - Camel (deleted): <https://www.printables.com/model/1282015-camel-low-poly>
  - Camel sitting, Mary, Joseph, donkey, cow: <https://www.printables.com/model/667692-nativity-scene>

Miscellaneous:

  - Amphora: <https://www.printables.com/model/817126-roman-clay-amphora>
  - Treasure Chest: <https://www.printables.com/model/12111-treasure-chests-for-gloomhaven>

Further Reading
---------------

Head on to [Support PCB](./pcb.md) to read about the optional pcb used
to simplify wiring.

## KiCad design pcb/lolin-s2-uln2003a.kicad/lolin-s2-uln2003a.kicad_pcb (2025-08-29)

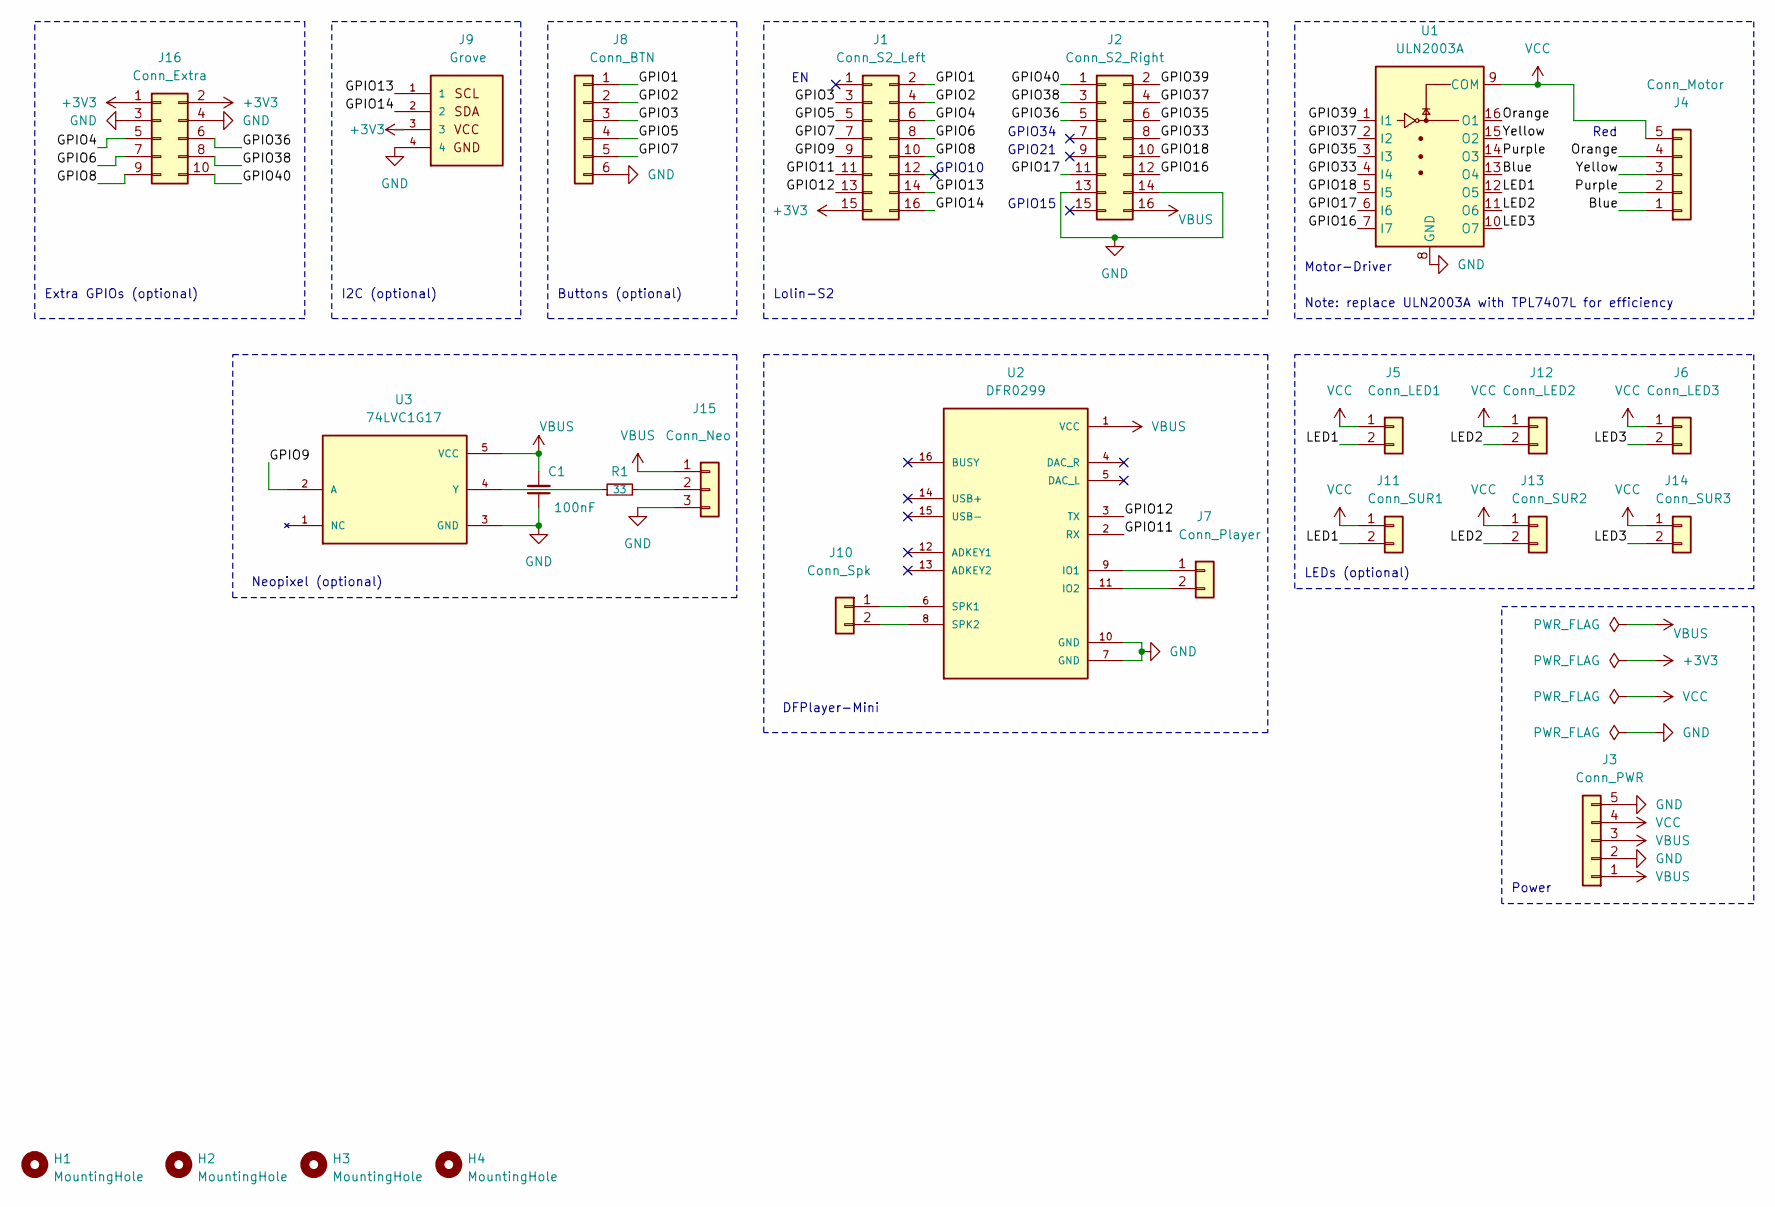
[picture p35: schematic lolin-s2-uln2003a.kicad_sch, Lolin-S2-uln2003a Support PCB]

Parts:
C1: 100nF; C_0402_1005Metric; LCSC C1525
H1, H2, H3, H4: MountingHole; MountingHole_2.5mm
J1: Conn_S2_Left; PinSocket_2x08_P2.54mm_Vertical
J2: Conn_S2_Right; PinSocket_2x08_P2.54mm_Vertical
J3: Conn_PWR; PinHeader_1x05_P2.54mm_Vertical
J4: Conn_Motor; JST_XH_B5B-XH-A_1x05_P2.50mm_Vertical
J5: Conn_LED1; JST_XH_B2B-XH-A_1x02_P2.50mm_Vertical
J6: Conn_LED3; JST_XH_B2B-XH-A_1x02_P2.50mm_Vertical
J7: Conn_Player; JST_XH_B2B-XH-A_1x02_P2.50mm_Vertical
J8: Conn_BTN; PinHeader_1x06_P2.54mm_Vertical
J9: Grove; grove_horizontal
J10: Conn_Spk; JST_XH_B2B-XH-A_1x02_P2.50mm_Vertical
J11: Conn_SUR1; JST_SUR_BM02B-SURS-TF_1x02-1MP_P0.80mm_Vertical; LCSC C385130
J12: Conn_LED2; JST_XH_B2B-XH-A_1x02_P2.50mm_Vertical
J13: Conn_SUR2; JST_SUR_BM02B-SURS-TF_1x02-1MP_P0.80mm_Vertical; LCSC C385130
J14: Conn_SUR3; JST_SUR_BM02B-SURS-TF_1x02-1MP_P0.80mm_Vertical; LCSC C385130
J15: Conn_Neo; JST_XH_B3B-XH-A_1x03_P2.50mm_Vertical
J16: Conn_Extra; PinHeader_2x05_P2.54mm_Vertical
R1: 33; R_0402_1005Metric; LCSC C25105
U1: ULN2003A; SOP-16_3.9x9.9mm_P1.27mm; LCSC C7512
U2: DFR0299
U3: 74LVC1G17; 74LVC1G17GW_125; LCSC C426705

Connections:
+3V3: J1.15, J9.3, J16.1, J16.2
/Blue: J4.1, U1.13 (O4)
/GPIO1: J1.2, J8.1
/GPIO2: J1.4, J8.2
/GPIO3: J1.3, J8.3
/GPIO4: J1.6, J16.5
/GPIO5: J1.5, J8.4
/GPIO6: J1.8, J16.7
/GPIO7: J1.7, J8.5
/GPIO8: J1.10, J16.9
/GPIO9: J1.9, U3.2 (A)
/GPIO11: J1.11, U2.2 (RX)
/GPIO12: J1.13, U2.3 (TX)
/GPIO13: J1.14, J9.1
/GPIO14: J1.16, J9.2
/GPIO16: J2.12, U1.7 (I7)
/GPIO17: J2.11, U1.6 (I6)
/GPIO18: J2.10, U1.5 (I5)
/GPIO33: J2.8, U1.4 (I4)
/GPIO35: J2.6, U1.3 (I3)
/GPIO36: J2.5, J16.6
/GPIO37: J2.4, U1.2 (I2)
/GPIO38: J2.3, J16.8
/GPIO39: J2.2, U1.1 (I1)
/GPIO40: J2.1, J16.10
/LED1: J5.2, J11.2, U1.12 (O5)
/LED2: J12.2, J13.2, U1.11 (O6)
/LED3: J6.2, J14.2, U1.10 (O7)
/Orange: J4.4, U1.16 (O1)
/Purple: J4.2, U1.14 (O3)
/Yellow: J4.3, U1.15 (O2)
GND: C1.1, J2.13, J2.14, J3.2, J3.5, J8.6, J9.4, J15.3, J16.3, J16.4, U1.8 (GND), U2.7 (GND), U2.10 (GND), U3.3 (GND)
unnamed: J7.1, U2.9 (IO1)
unnamed: J7.2, U2.11 (IO2)
unnamed: J10.1, U2.6 (SPK1)
unnamed: J10.2, U2.8 (SPK2)
unnamed: J15.2, R1.2
unnamed: R1.1, U3.4 (Y)
VBUS: C1.2, J2.16, J3.1, J3.3, J15.1, U2.1 (VCC), U3.5 (VCC)
VCC: J3.4, J4.5, J5.1, J6.1, J11.1, J12.1, J13.1, J14.1, U1.9 (COM)

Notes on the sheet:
Lolin-S2
Buttons (optional)
Note: replace ULN2003A with TPL7407L for efficiency
Motor-Driver
Neopixel (optional)
GPIO21
GPIO34
GPIO10
Red
Power
Extra GPIOs (optional)
GPIO15
DFPlayer-Mini
LEDs (optional)
I2C (optional)

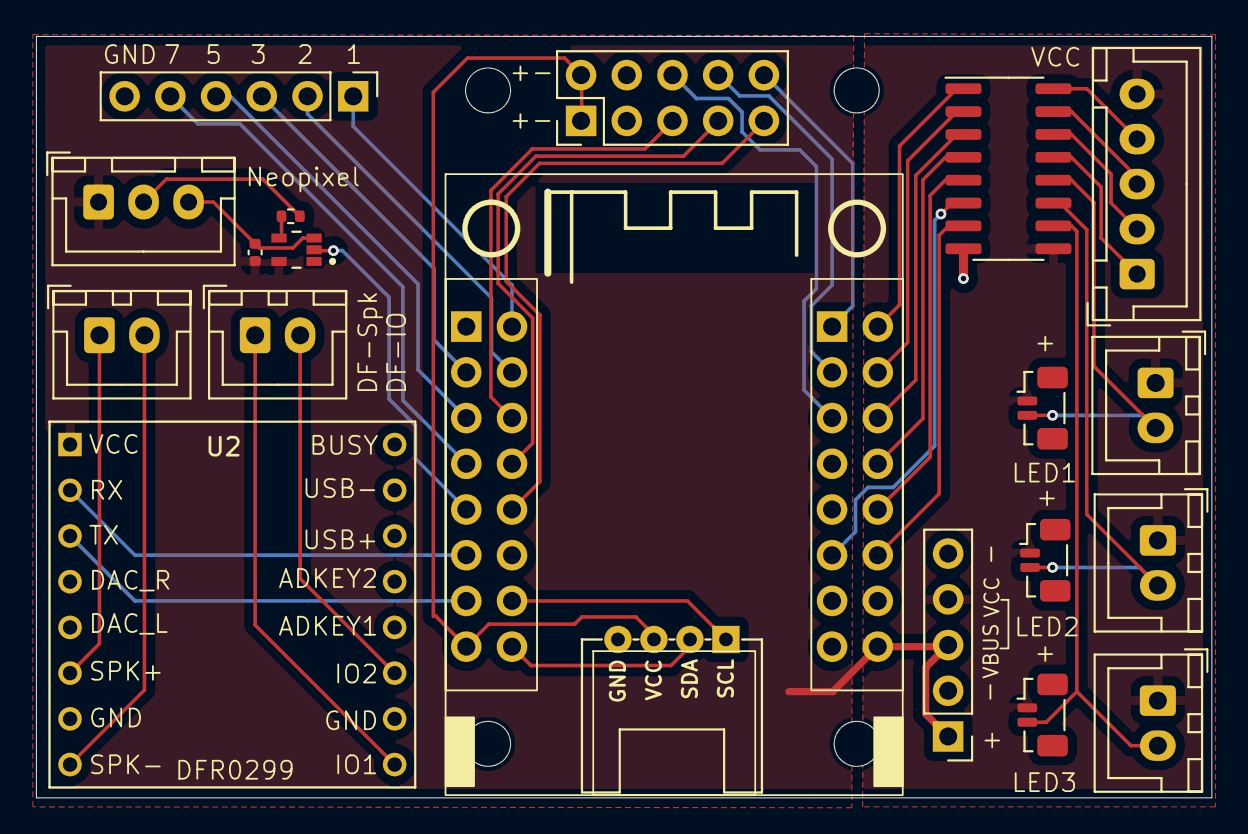
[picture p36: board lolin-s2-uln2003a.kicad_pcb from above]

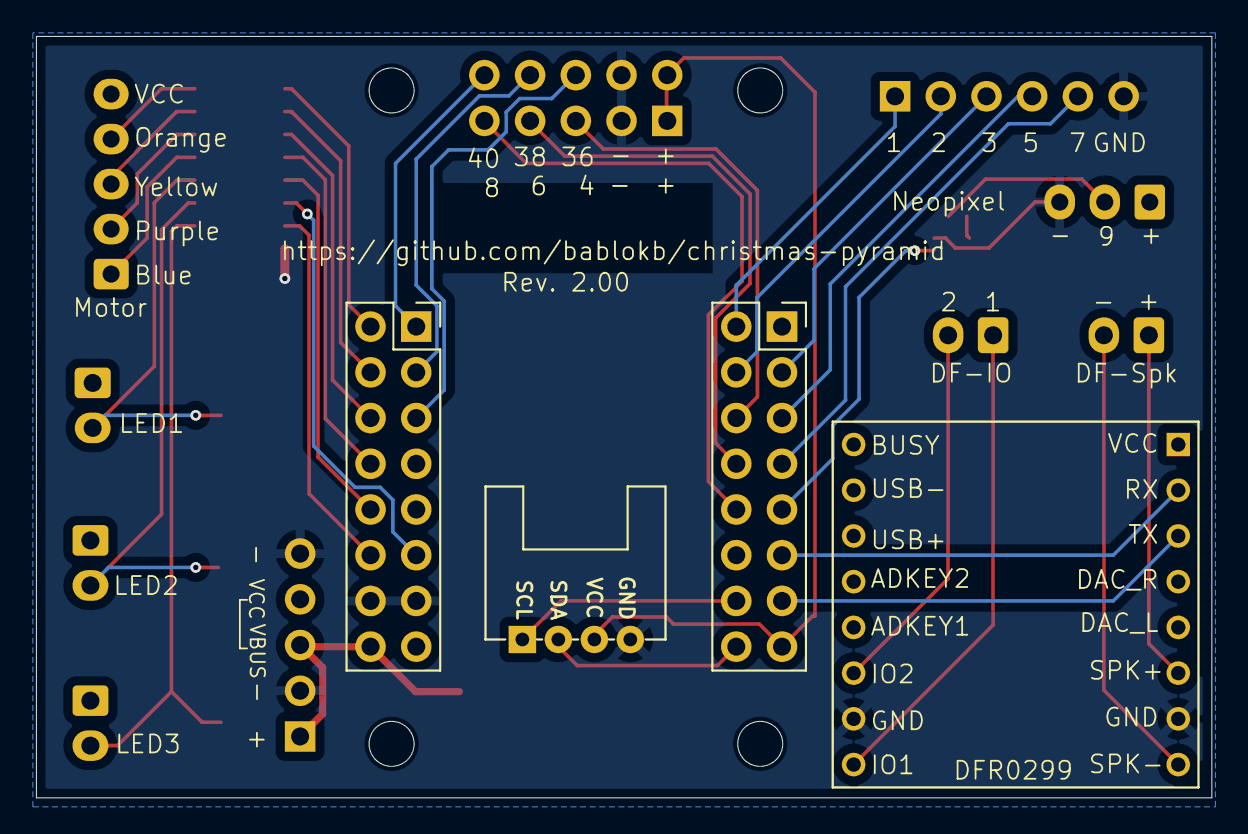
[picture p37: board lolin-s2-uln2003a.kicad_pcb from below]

Board: 2 copper layers, 65.3 x 42.3 mm, 25 parts (2 on the bottom side), 40 nets.

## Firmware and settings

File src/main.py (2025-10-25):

# ----------------------------------------------------------------------------
# Main program.
#
# Author: Bernhard Bablok
# License: GPL3
#
# Website: https://github.com/bablokb/christmas-pyramid
# ----------------------------------------------------------------------------

import supervisor
import time
import board
import asyncio

from motor import Motor
from player import Player
from leds import Leds
from neos import Neos
from buttons import Buttons

# --- configuration   --------------------------------------------------------

#import config_breadboard as config
#import config_simple as config
import config_pcb as config

# --- main task   ------------------------------------------------------------

_stop_event = asyncio.Event()
async def main():
  """ main co-routine """

  # individual controller objects and tasks
  # tasks is a list of (obj,initial-delay)-pairs
  tasks = []
  if config.WITH_MOTOR:
    motor = Motor(config.PINS_MOTOR,
                  config.GEAR_RATIO,
                  config.DIRECTION,
                  config.RPM,
                  config.DEBUG)
    tasks.append((motor,0))
  else:
    motor = None

  if config.WITH_PLAYER:
    player = Player(config.PINS_UART, config.VOLUME, config.DEBUG)
    tasks.append((player,0.2))
  else:
    player = None

  if config.WITH_BUTTONS:
    buttons = Buttons(config.PINS_BUTTON, config.PINS_CB,
                      motor, player, config.DEBUG)
    tasks.append((buttons,0))

  if config.WITH_LEDS:
    leds = Leds(config.PINS_LED, config.DUTY_LED, config.DEBUG)
    tasks.append((leds,0.5))

  if config.WITH_NEOPIXEL:
    neos = Neos(config.PINS_NEO, config.DUTY_NEO, config.DEBUG)
    tasks.append((neos,0.5))
  else:
    neos = None

  # start configured controller tasks and wait for end
  if config.DEBUG:
    print("starting controller tasks")
  coprocs = [t[0].run(t[1],_stop_event) for t in tasks]

  await asyncio.gather(*coprocs)

# --- cleanup task   ---------------------------------------------------------

async def terminate():
  """ wait for task termination """
  if config.DEBUG:
    print("running terminate()...")
  _stop_event.set()
  await asyncio.sleep(3)
  if config.DEBUG:
    print("finished terminate()")

# --- main program   ---------------------------------------------------------

if config.DEBUG:
  start = time.monotonic()
  while (not supervisor.runtime.serial_connected and
         time.monotonic() < start + config.WAIT4CONSOLE):
    time.sleep(1)

try:
  asyncio.run(main())
except KeyboardInterrupt:
  if config.DEBUG:
    print(f"interrupted!")
except Exception as ex:
  if config.DEBUG:
    print(f"exception: {ex}")
finally:
  asyncio.run(terminate())

if config.DEBUG:
  print("done running main")

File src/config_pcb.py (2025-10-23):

# ----------------------------------------------------------------------------
# Pin configuration for PCB.
#
# Author: Bernhard Bablok
# License: GPL3
#
# Website: https://github.com/bablokb/christmas-pyramid
# ----------------------------------------------------------------------------

import board
from uln2003a import GEAR_RATIO_64
from buttons import CB_SLOWER, CB_FASTER, CB_PREV, CB_PAUSE, CB_NEXT

# --- setup   ----------------------------------------------------------------

GEAR_RATIO   = GEAR_RATIO_64
DIRECTION    = -1
RPM          = 6
DEBUG        = False
WAIT4CONSOLE = 5      # in debug-mode, wait x secs for console

WITH_MOTOR    = True
WITH_PLAYER   = True
WITH_LEDS     = True
WITH_BUTTONS  = True
WITH_NEOPIXEL = False

# --- pin definitions   ------------------------------------------------------

# I2C
PIN_SCL = board.IO13
PIN_SDA = board.IO14

# DFPlayer
PINS_UART = [board.IO11, board.IO12]  # TX, RX
VOLUME    = 80

# SD-card (SPI, unused for DFPlayer)
PINS_SD = [
  board.IO10,  # MISO
  board.IO6,   # MOSI
  board.IO8,   # CLK
  board.IO4,   # CS
]

# motor GPIOs
PINS_MOTOR = [board.IO39,board.IO37,board.IO35,board.IO33]

# LED GPIOs
PINS_LED = [board.IO18,board.IO17,board.IO16]
DUTY_LED = [0.5,0.5,0.5]

# NEO PINs (unused)
PINS_NEO = (None,0)
DUTY_NEO = 0.1

# I2S (unused for DFPlayer)
PIN_MUTE   = board.IO38
PINS_I2S   = [board.IO11,board.IO12,board.IO9,PIN_MUTE] # BLCK, WSEL, DATA

# Buttons (audio next/volup and prev/voldown are handled directly by DFPlayer)
PINS_BUTTON = [
  board.IO7,    # slower
  board.IO5,    # faster
  board.IO3,    # pause
]
PINS_CB = [CB_SLOWER, CB_FASTER, CB_PAUSE]

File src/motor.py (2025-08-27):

# ----------------------------------------------------------------------------
# Class Motor links to the motor-driver and keeps state.
#
# Author: Bernhard Bablok
# License: GPL3
#
# Website: https://github.com/bablokb/christmas-pyramid
# ----------------------------------------------------------------------------

import asyncio
import uln2003a

from base import Base

class Motor(Base):
  """ Controller of motor-driver """

  # --- constructor   --------------------------------------------------------

  def __init__(self, pins,
               gear_ratio=uln2003a.GEAR_RATIO_16,
               direction=1,
               rpm=0,
               debug=False):
    """ constructor """

    super().__init__(debug)
    self._pins = pins
    self._gear_ratio = gear_ratio
    self._direction = direction
    self._rpm = rpm
    self._motor = None
    self.running = False

  # --- motor task   ---------------------------------------------------------

  async def run(self, delay, stop_event):
    """ create motor task """

    await asyncio.sleep(delay)
    self._motor = uln2003a.Uln2003aFullStep(*self._pins,
                                            self._gear_ratio,
                                            debug=self._debug)
    self._msg("starting rotation")
    asyncio.create_task(self._motor.rotate(self._direction,self._rpm))
    self._msg("motor: waiting for stop")
    await stop_event.wait()
    self._msg("stopping rotation")
    self._motor.stop()
    self._motor.deinit()

  # --- change RPM   ---------------------------------------------------------

  def inc_rpm(self,delta):
    """ change RPM value """

    self._msg(f"inc_rpm({delta})")
    if self._motor:
      self._motor.inc_rpm(delta)

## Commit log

2025-06-16 Rev. 1.00 files for motor-pcb
    [BOM-lolin-s2-uln2003a.csv, lolin-s2-uln2003a.kicad_pcb, lolin-s2-uln2003a.kicad_sch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]
2025-06-17 first draft base of pyramid
    [base.scad, dimensions.scad, shared.scad]
2025-06-17 change inner diameter of motor-support
    [shared.scad]
2025-06-17 set base-size to 85
    [shared.scad]
2025-06-17 fix position of pcb-holder
    [base.scad]
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2025-06-20 add cutout for SD-card
    [pcb_holder.scad]
2025-06-20 use parameters for wall-cutout
    [shared.scad]
2025-06-20 add wall-cutout, fix pcb-holder orientation
    [base.scad]
2025-06-20 post(): use cyl for preview and star for final rendering
    [base.scad]
2025-06-20 fine-tune cutouts, cone and total height
    [base.scad, shared.scad]
2025-06-24 added cutout for LED-cable from base to first level
    [base.scad]
2025-06-27 add models for base-level walls
    [base_walls.scad]
2025-06-27 model for LED-strips (for background lighting)
    [led-strip-holder.scad]
2025-06-28 wall_pcb(): add cutouts for air-flow
    [base_walls.scad]
2025-06-28 add cutout for air-flow
    [base.scad]
2025-06-28 tilt cutout for LED-cable
    [base.scad]
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2025-07-07 add cutout for motor-cable
    [led-strip-holder.scad]
2025-07-07 fix: post(): add cone alignment to BOTTOM+CENTER
    [base.scad]
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2025-07-10 add cutouts to outer posts and cutouts to floor
    [level1.scad]
2025-07-10 add dimensions for level1
    [shared.scad]
2025-07-10 first iteration fences for level1
    [level1_fences.scad]
2025-07-11 fence-posts: only cutout upper third to increase stability
    [level1.scad]
2025-07-11 add cutout height for fence-posts
    [shared.scad]
2025-07-11 add cutouts for fences because cutout of posts are no longer full height
    [level1_fences.scad]
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2025-07-14 add button-holder to wall_pcb()
    [base_walls.scad]
2025-07-14 fine tune inner cutout fence-post
    [level1.scad]
2025-07-16 fine-tune cutout for USB-C
    [base_walls.scad]
2025-07-16 add some more cutout-depth for fences (simplify 3D-printing)
    [level1.scad]
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2025-07-18 fence-post: fine-tune cutout for base-cone
    [level1.scad]
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2025-07-19 reordered base-plate objects; added module lamp_shade()
    [level1.scad]
2025-07-19 fine tune fence-post cutout again
    [level1.scad]
2025-07-21 refactored turntable-plate to tt_plate.scad
    [level1.scad, tt_plate.scad]
2025-07-21 change from 6 to 4 level1-posts
    [level1.scad]
2025-07-21 refactor dimensions from tt_plate.scad to shared.scad
    [shared.scad, tt_plate.scad]
2025-07-22 move level1-posts to the center
    [shared.scad]
2025-07-22 cutouts for level1-posts only in the upper third
    [level1.scad]
2025-07-22 fix next/prev file-switching
2025-07-23 added nativity-fence; fine-tune all fences
    [level1_fences.scad]
2025-07-24 add dimensions for level1 walls
    [shared.scad]
2025-07-24 replace hard-coded values with values from shared.scad
    [level1.scad]
2025-07-24 designed walls for level1
    [level1_walls.scad]
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2025-07-30 initial implementation of level2
    [level2.scad, level2_fence.scad]
2025-08-02 fix: expose inc_rpm() instead of set_rpm()
    [motor.py]
2025-08-02 fix: don't switch to next song when current song was interrupted
    [player.py]
2025-08-08 reduce level2 fence height
    [shared.scad]
2025-08-08 add cutout for cable
    [level2_fence.scad]
2025-08-14 add cutouts for all posts
    [level2_fence.scad]
2025-08-14 add cutouts for central plate, hole and cable
    [level2.scad]
2025-08-14 add a central plate
    [level2.scad]
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2025-08-25 fixed gain-labels on F.Silkscreen
    [lolin-s2-uln2003a.kicad_pcb]
2025-08-25 fixed rotation of motor-connector
    [lolin-s2-uln2003a.kicad_pcb, lolin-s2-uln2003a.kicad_sch]
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2025-08-25 update after fixing unsymmetric mounting holes
    [shared.scad]
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2025-08-25 update due to production-file generation
    [lolin-s2-uln2003a.kicad_pcb]
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2025-08-29 Rev. 2.00 of support-pcb
    [BOM-lolin-s2-uln2003a.csv, lolin-s2-uln2003a.kicad_pcb, lolin-s2-uln2003a.kicad_sch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]
2025-09-09 pcb_holder: updated screw-offsets for Rev 2.00 board
    [shared.scad]
2025-09-09 larger offset for cable-holders
    [base.scad]
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2025-09-11 adapt for Rev 2.00 PCB
    [pcb_holder.scad]
2025-09-17 flip orientation of button-holder
    [button_holder.scad]
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2025-09-17 added model-files for silhouettes/cutouts
    [angel_praying.stl, angel_trompet.stl, camel.stl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]
2025-09-18 pcb_holder(): refactor special supports to pcb_holder_special() (and use this in base.scad)
    [base.scad, pcb_holder.scad]
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2025-09-22 fix: pause(): toggle self._playing
    [player.py]
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2025-09-25 design change: higher, with cutouts for spots
    [level2.scad]
2025-09-26 fixed size of cutouts for spots
    [level2.scad]
2025-09-26 refactoring: move code for cable-channels to module c_channels()
    [level2.scad]
2025-09-26 redesign: move cable-channels to level2
    [level2.scad]
2025-09-26 increased size of level2-posts/level2-fence
    [shared.scad]
2025-09-27 initial version simple base
    [simple_base.scad]
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2025-09-27 refactored motor-dimensions to motor_dims.scad
    [motor_dims.scad, shared.scad]
2025-09-27 doubled height of motor-posts
    [simple_base.scad]
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2025-09-27 added holder for speaker
    [simple_base.scad]
2025-09-29 refactoring: move shared dimensions to simple_shared.scad
    [simple_base.scad, simple_shared.scad]
2025-09-29 initial design simple wall
    [simple_wall.scad]
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2025-09-29 redesign (more FDM-friendly)
    [simple_wall.scad]
2025-09-30 optimize height, add comments
    [simple_wall.scad]
2025-09-30 change top-most ring to a inverted cone
    [simple_wall.scad]
2025-09-30 add more strength to motor-posts
    [simple_base.scad]
2025-10-03 refactored top-diameter to simple_shared.scad
    [simple_shared.scad, simple_wall.scad]
2025-10-03 refactoring: make tt_plate a reusable module
    [level1.scad, tt_plate.scad]
2025-10-04 fix: add .forever() to candle()
    [leds.py]
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2025-10-08 support a variable number of buttons
    [button_holder.scad]
2025-10-08 pass number of buttons to button_holder()
    [base_walls.scad]
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2025-10-09 initial design for turn-table plate for simple-base
    [simple_plate.scad]
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2025-10-09 print with or without button-holder
    [simple_wall.scad]
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2025-10-15 revert simple_wall to version without button-holder
    [simple_wall.scad]
2025-10-15 DFPlayer: shrink cutout+lid of second cutout
    [simple_base.scad]
2025-10-15 DFPlayer: shrink first cutout to match second cutout
    [simple_base.scad]
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2025-10-15 revert simple_base.scad (no button-holder, large DFPlayer cutout)
    [simple_base.scad]
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
